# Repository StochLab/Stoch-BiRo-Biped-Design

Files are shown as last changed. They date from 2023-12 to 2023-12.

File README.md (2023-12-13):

# Design of Stoch BiRo (Bipedal Robot)

This repository provides the design files for [Stoch-BiRo](https://tayalmanan28.github.io/Stoch-BiRo/) [(Paper)](https://arxiv.org/pdf/2312.06512.pdf)

<div align="center">
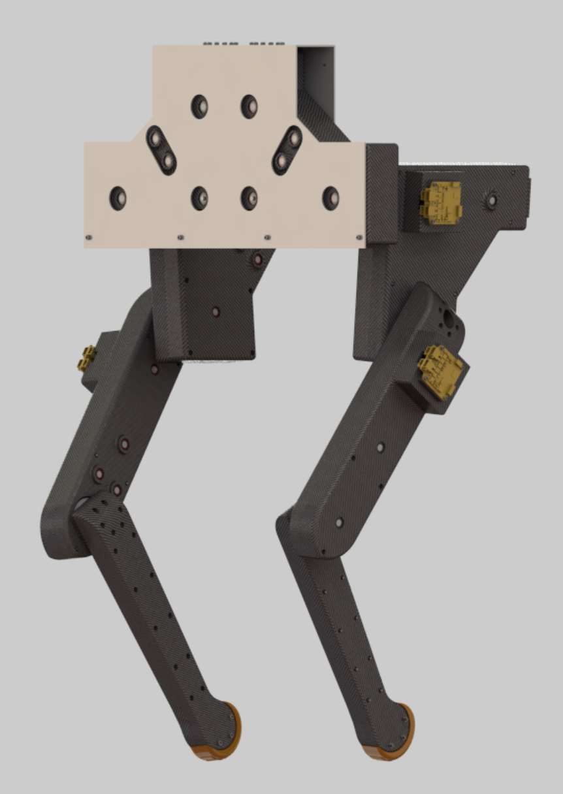
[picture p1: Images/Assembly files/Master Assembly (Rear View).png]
  <br>
<!--   <strong>Stoch BiRo</strong> -->
</div>

The Biped consists of a Torso and two 3-DOF Legs as described below:

<div align="center">
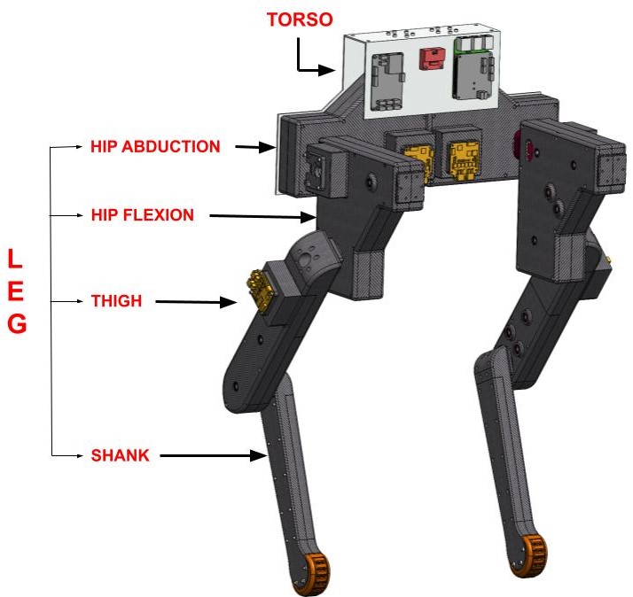
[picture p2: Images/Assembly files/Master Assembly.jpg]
  
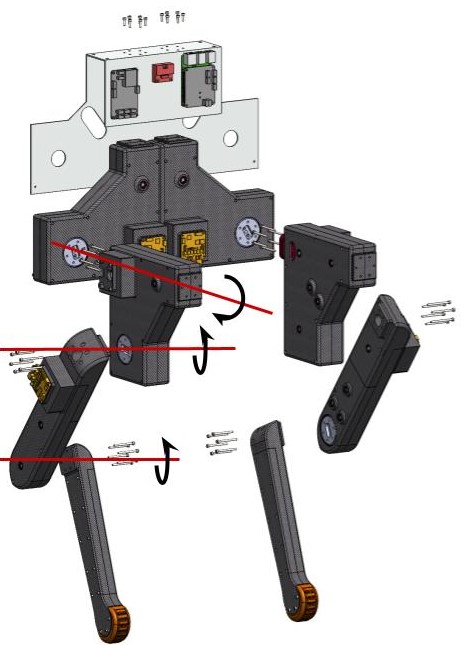
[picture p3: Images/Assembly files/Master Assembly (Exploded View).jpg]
    
</div>

## Torso

The torso consists of two L-shaped aluminum plates bolted together. The torso contains the Power Distribution Board, Raspberry Pi + Pi3Hat for on board compute, and sensors like Xsens MTi-610 IMU. 

## 3 DOF Leg

The hip actuator modules for both legs are mirrored versions of each other. 

**NOTE:** *The components in the actuation modules are denoted in the images below as follows:*

<div class="tg-wrap" align="center"><table align="center" style="margin: 0px auto;"><tbody><tr align="center"><td><strong>A.</strong></td><td><strong>B.</strong></td><td><strong>C.</strong></td><td><strong>D.</strong></td><td><strong>E.</strong></td><td><strong>F.</strong></td></tr><tr align = "center"><td>T-Motor Antigravity MN5006 BLDC Motor</td><td>Motor coupling</td><td>Stage-I HTD Pulley (13 Teeth)</td><td>MJBOTS Moteus r4.11 driver</td><td>HTD Timing Belts</td><td>Stage-II HTD Pulley (13 Teeth)</td></tr><tr align="center"><td><strong>G.</strong></td><td><strong>H.</strong></td><td><strong>I.</strong></td><td><strong>J.</strong></td><td><strong>K.</strong></td></tr><tr align = "center"><td>Stage-I HTD Pulley (39 Teeth)</td><td>Roller Tensioners</td><td>Stage-II HTD Pulley (39 Teeth)</td><td>Joint coupling</td><td> Hip-to-hip attachment</td></tr></tbody></table></div>

### Abduction Module

The abduction module is the topmost module of a leg in the biped. It is responsible for the abduction and adduction movement of the robot's hip, similar to that of humans. The module is attached to the torso plate and the motor drives the belts and pulleys with the output pulley attached to the abduction-flexion coupling. This coupling is a part of the abduction joint, which connects the abduction and the flexion modules. Tensioners are provided to prevent any slack in the timing belts while running.

<div align="center">
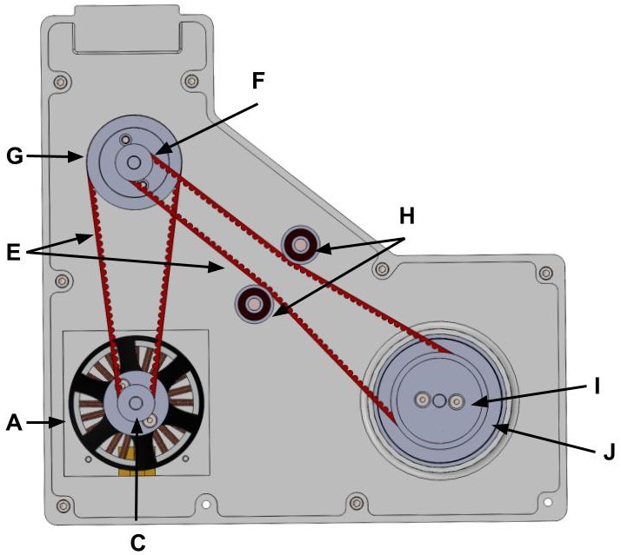
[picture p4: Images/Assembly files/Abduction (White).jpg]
  <br>
  <strong>Abduction Module</strong>
</div>

### Hip Flexion Module

The hip flexion module is placed between the hip abduction and thigh modules. This module is similar to that of the abduction module with few changes. It performs the flexion-extension motion. The motion of this module is controlled by the abduction motor and the motor in the flexion module controls the flexion joint, which connects the flexion and thigh modules. This module consists of a hip-to-hip attachment and the abduction-flexion coupling in the abduction module is fastened to it during assembly for transmitting the motion. The output pulley is connected to a flexion-thigh coupling. This coupling forms the flexion joint, which connects the flexion and thigh modules.

<div align="center">
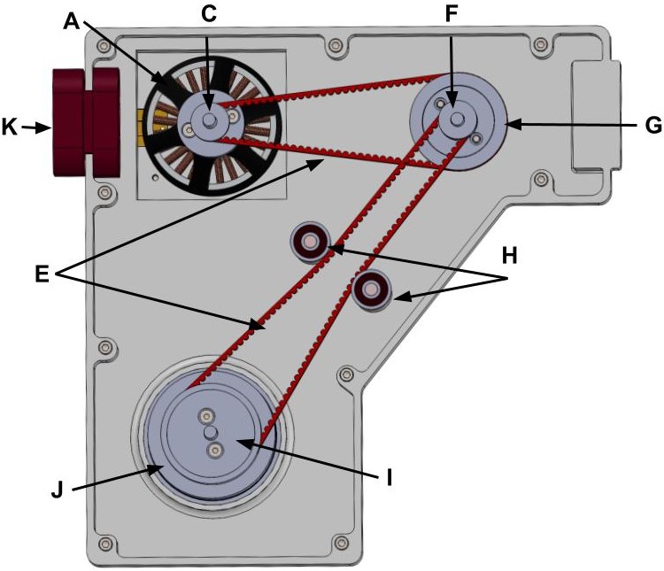
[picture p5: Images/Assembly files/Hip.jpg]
  <br>
  <strong>Hip Flexion Module</strong>
</div>

### Thigh Module

The thigh module is responsible for the knee motion of the biped, similar to the primary movement of human knees. The flexion joint controls the movement of this module. The motor of the thigh module, together with the dual-stage reduction using belts and pulleys, controls the knee joint. The thigh joint comprises a thigh-shank coupling, which is the same as that of the flexion-thigh coupling. The output pulley is attached to this coupling and the motion is transmitted to the shank module. Unlike the previous two modules which had a triangular configuration, the belts of this module are arranged linearly.

<div align="center">
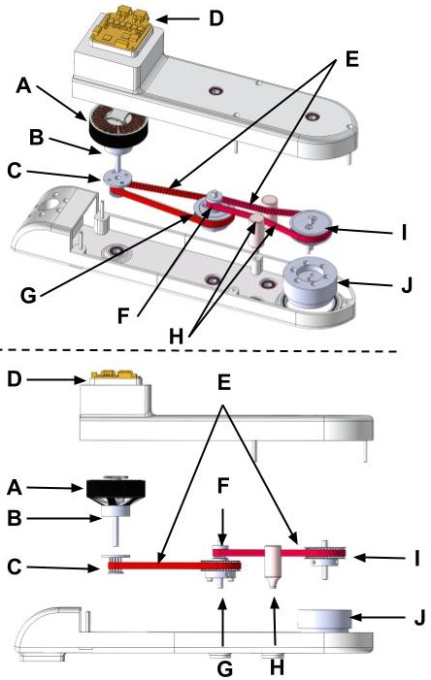
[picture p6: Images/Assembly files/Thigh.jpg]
  <br>
  <strong>Thigh Module</strong>
</div>

Internal components of the actuator modules are described here: 

- [Mechanical Components](https://github.com/StochLab/Stoch-BiRo-Biped-Design/blob/main/Mechanical%20components.md)
- [Electrical Components and Sensor Details](https://github.com/StochLab/Stoch-BiRo-Biped-Design/blob/main/Electrical%20Components.md)

### Shank

As the name suggests, the shank is the lowest part of the biped leg, which runs from the knee to the foot. The motor of the thigh controls its movement at the knee joint. A single-point contact foot made of polyurethane (PU) is attached to the end of the shank for better grip of the biped when in contact with a surface. This module is similar to the structure of the thigh but without any of the actuating components (motors, belts, pulleys, etc.) and with a provision for foot attachment at its bottom end.

<div align="center">
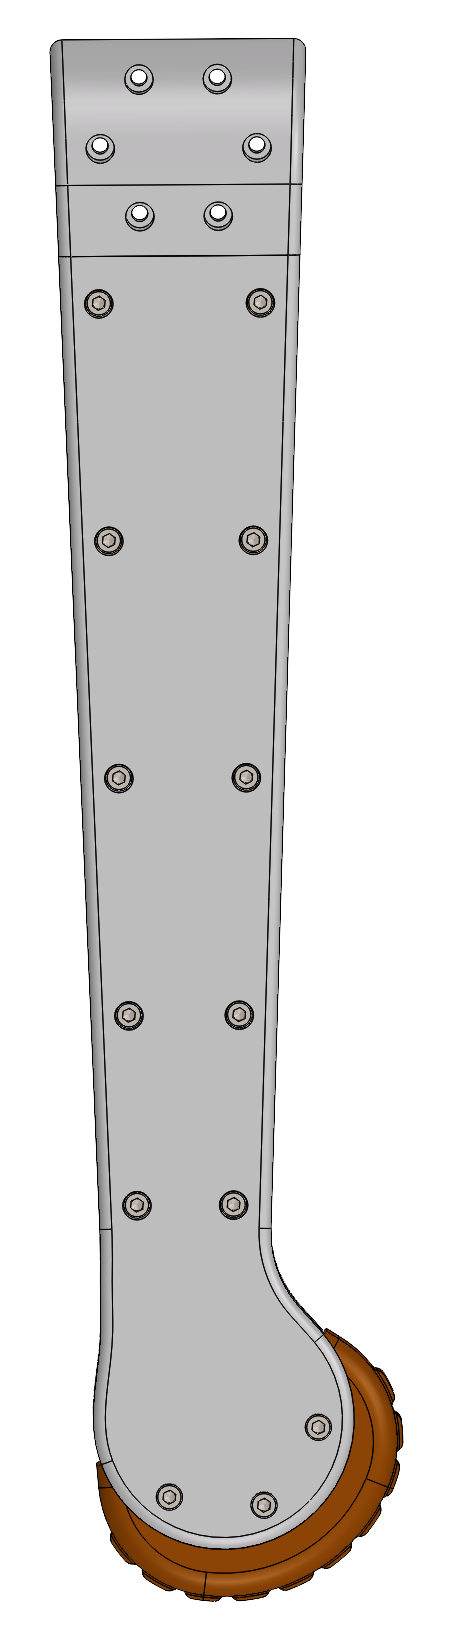
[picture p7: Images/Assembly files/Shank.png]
  <br>
  <strong>Shank</strong>
</div>

# Citation

If you use these designs and/or Stoch BiRo in your work please cite this paper with:

```
@misc{mothish2023stoch,
      title={Stoch BiRo: Design and Control of a low cost bipedal robot}, 
      author={GVS Mothish and Karthik Rajgopal and Ravi Kola and Manan Tayal and Shishir Kolathaya},
      year={2023},
      eprint={2312.06512},
      archivePrefix={arXiv},
      primaryClass={cs.RO}
}
```

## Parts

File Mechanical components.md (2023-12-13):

## Timing Belts and Pulleys:

HTD Timing belts made of Neoprene Rubber With Fiberglass Core, along with timing pulleys made of Aluminium, are responsible for increasing the torque by nine times. As the pulleys have 20 teeth and 60 teeth, two pairs of pulleys are used consecutively for an overall gear reduction of 9:1 with a 3:1 reduction at each stage. The HTD pulleys were 3D printed with an extra fine layer height of 0.1mm and 90\% infill density with PLA material and PVA (Polyvinyl acetate) supports as it is water soluble which facilitates support removal without any effect on the quality of tooth profile.

<div class="tg-wrap" align="center"><table align="center" style="margin: 0px auto;"><thead><tr><th colspan="6">HTD Timing Belts</th></tr></thead><tbody><tr align = "center"><td>Sl. No. </td><td>Pitch</td><td>Width</td><td>Total Length</td><td>Belt Height</td><td>Tooth Height</td></tr><tr align = "center"><td>1.</td><td>3mm</td><td>6mm</td><td>279mm</td><td>2.4mm</td><td>1.17mm</td></tr><tr align = "center"><td>2.</td><td>3mm</td><td>6mm</td><td>399mm</td><td>2.4mm</td><td>1.17mm</td></tr></tbody></table></div>

<div class="tg-wrap" align="center"><table style="margin-left: auto; margin-right: auto;"><thead><tr><th colspan="4">HTD Pulleys</th></tr></thead><tbody><tr align = "center"><td>Sl. No. </td><td>Bore Diameter</td><td>Outer Diameter</td><td>No. of Teeth</td></tr><tr align = "center"><td>1.</td><td rowspan="4">5mm</td><td rowspan="2">16mm</td><td>13</td></tr><tr align = "center"><td>2.</td><td>14</td></tr><tr align = "center"><td>3.</td><td rowspan="2">44mm</td><td>39</td></tr><tr align = "center"><td>4.</td><td>42</td></tr></tbody></table></div>

## Bearings:

Deep groove ball bearings are used as they are easy to mount and can accommodate both axial and radial loads. They have low friction and are optimized for low noise and low vibration which enables high rotational speeds. These bearings have minimal service or maintenance. The deep grooves in the bearings enable axial loads to be carried in either direction.

<div class="tg-wrap" align="center"><table><thead><tr><th colspan="4">Bearings</th></tr></thead><tbody><tr align = "center"><td>Sl. No. </td><td>Inner Diameter</td><td>Outer Diameter</td><td>Width</td></tr><tr align = "center"><td>1.</td><td>5mm</td><td>16mm</td><td>5mm</td></tr><tr align = "center"><td>2.</td><td>45mm</td><td>55mm</td><td>5mm</td></tr></tbody></table></div>

## Roller Tensioners:

Two tensioners are provided in each module to avoid any slack in the timing belts during its motion. As the motors are engaged, slippage between the pulley teeth and the belt teeth is possible. Tensioners act as rollers and provide tension to the belts resulting in proper teeth engagement between the belts and the pulleys. The tensioners used for the biped are long cylindrical structures attached to the bearings in the cover parts of the modules, which have moving components. They are placed so that it doesn't interfere with the working of an actuating system. The narrower cylindrical section of the tensioner is attached to the ball bearing.

## Motor Couplings:

The custom-made motor coupling connects the motor to the pulleys. 4 countersunk screws of M3 size are used to tighten the motor coupling to the motor's rotor. The shaft is attached to the motor coupling and the pulley of 20 teeth is locked to the shaft. The threaded holes are 18mm apart diagonally and the shaft is 5mm in diameter. The material used is stainless steel, as aluminum parts tend to bend, and steel is three times stronger than aluminum. Since the motor coupling is responsible for transmitting power from the motor to the rest of the actuation module, it is necessary to have a stronger material for the motor coupling.

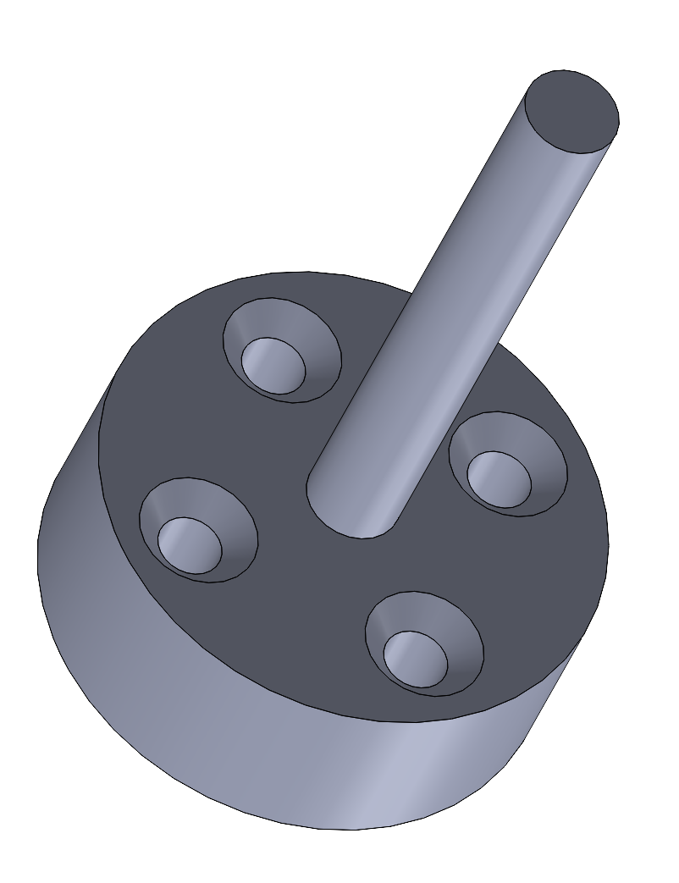
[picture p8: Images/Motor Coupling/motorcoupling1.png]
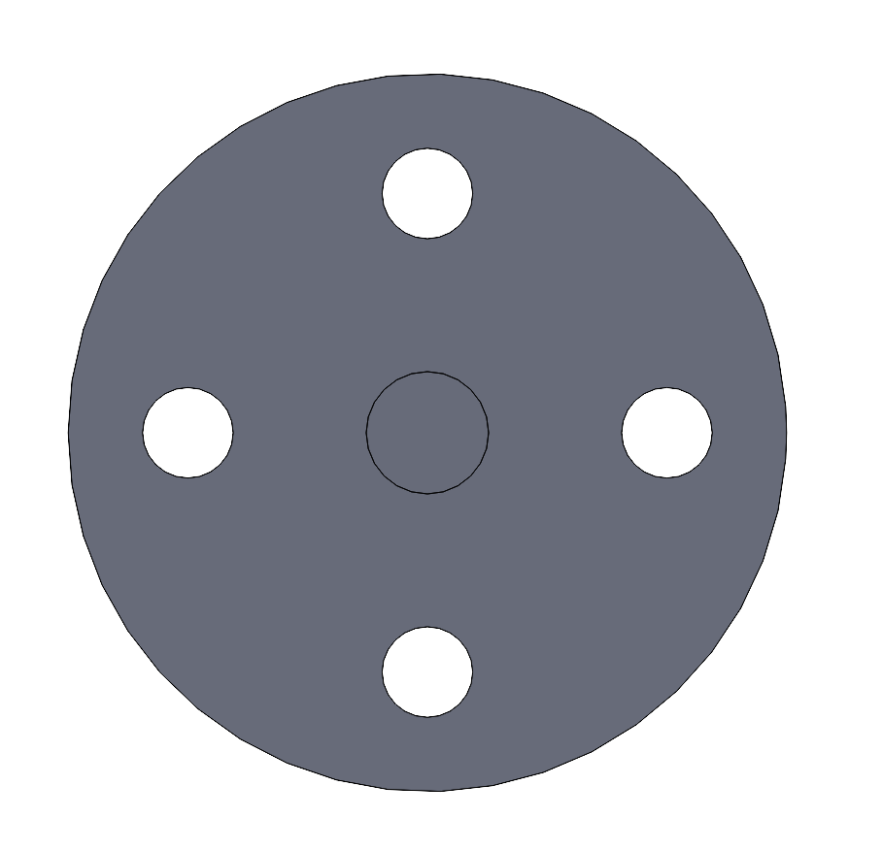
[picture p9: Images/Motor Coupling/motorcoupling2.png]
| |    |
|:---:|:---:|
|CAD Model|Rear View|

## Hip-to-hip attachment:

The hip-to-hip attachment, along with abduction-flexion coupling, connects the abduction module to the flexion module. Both modules are bolted to each other from the side of the abduction module. During the assembly of the modules, the hip-to-hip attachment is on the side of the flexion module and the abduction-flexion coupling is in the abduction module. Six M3 screws are bolted from the coupling's side to ensure proper rotation of the flexion module once the abduction motor is engaged. This part is put in a slit provided in the base part of the flexion module as a loose fit and once they are bolted, it will restrict any sort of relative motion with the flexion module resulting in a revolute joint between abduction and flexion modules.

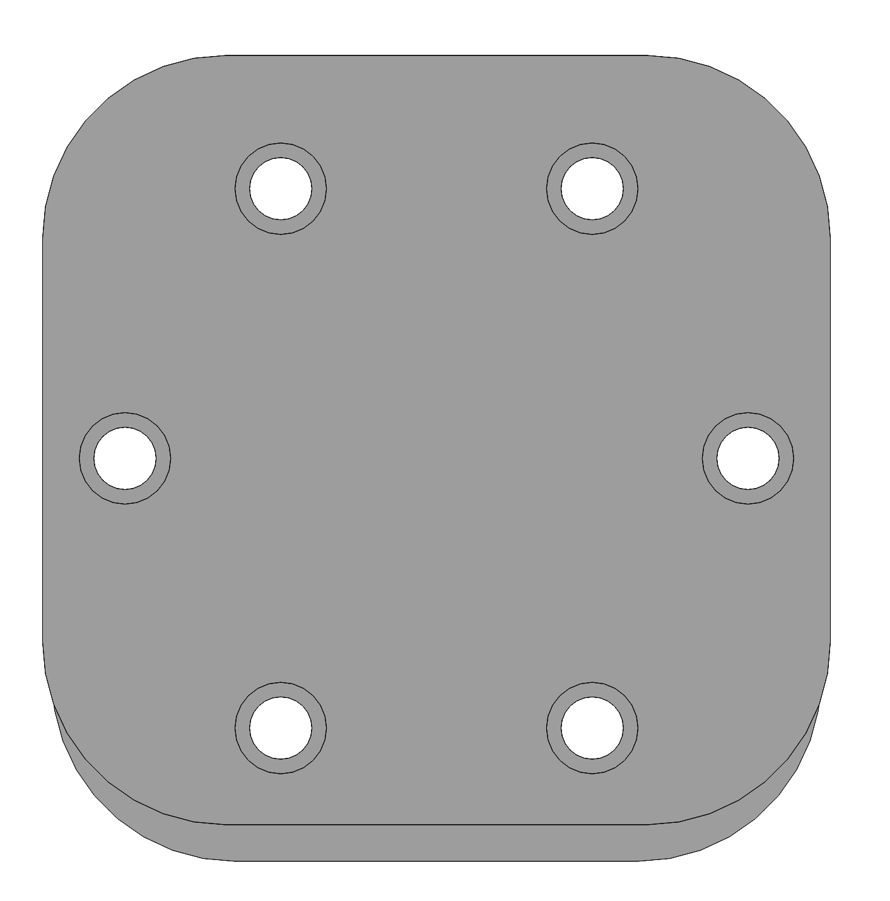
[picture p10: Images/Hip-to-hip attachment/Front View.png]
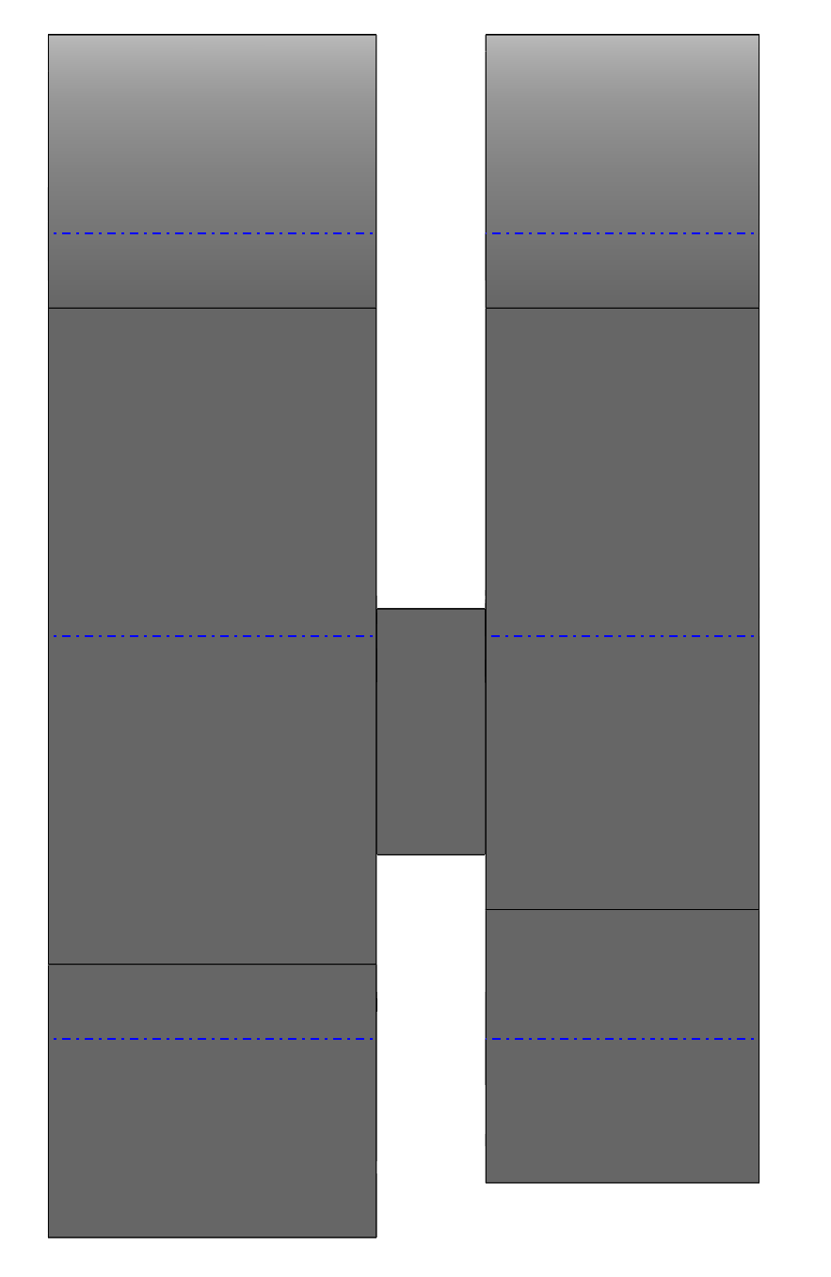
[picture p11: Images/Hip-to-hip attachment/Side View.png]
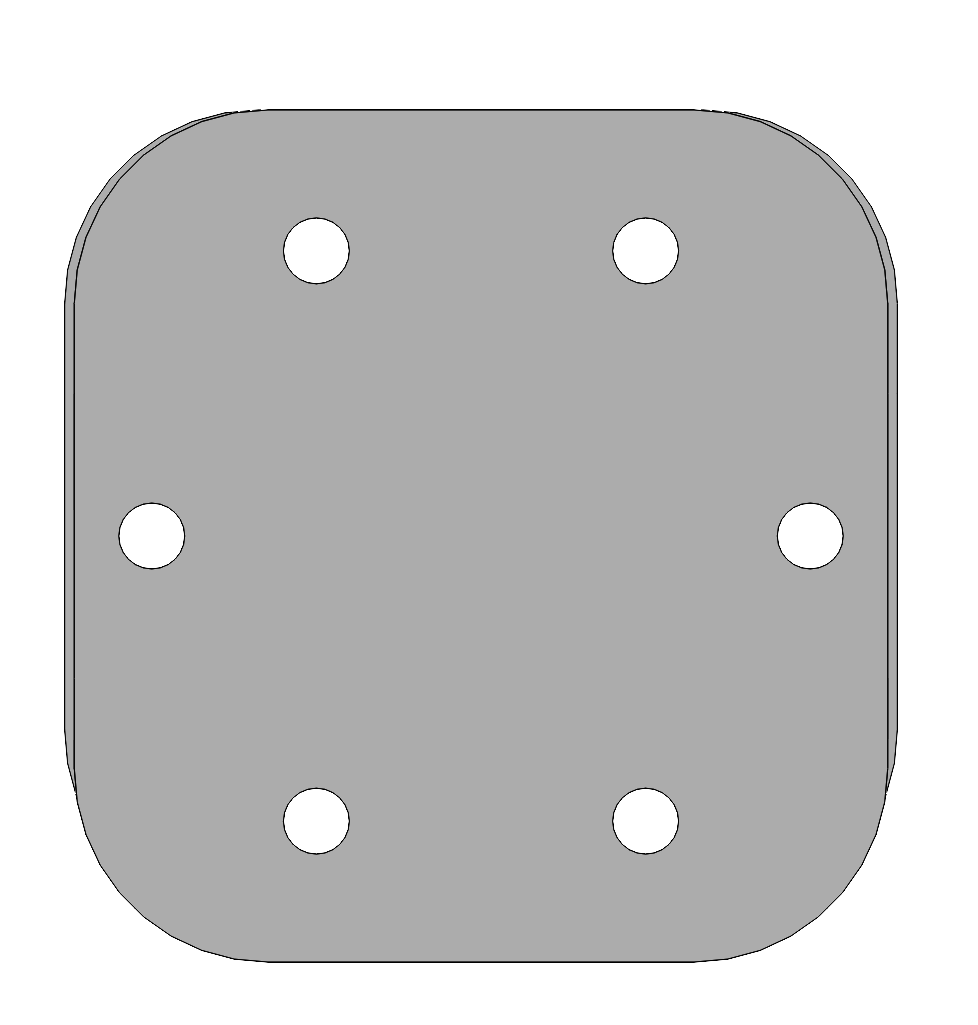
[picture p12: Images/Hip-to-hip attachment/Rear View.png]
| |    |  |
|:---:|:---:|:---:|
|Front View|Side View|Rear View|

## Joint Couplings:

The joint couplings are parts used to connect two actuator modules. Two such distinct couplings are used in the biped: abduction-flexion coupling and flexion-thigh coupling (thigh-shank coupling uses the same design). As the names suggest, abduction-flexion coupling acts as the joint between the hip abduction and flexion modules, flexion-thigh coupling as the joint between the hip flexion and thigh modules, and thigh-shank one as the joint between the thigh and shank modules. In all of them, the output pulley (the larger pulley of the second belt-pulley reduction stage) is bolted to the coupling using two M3 bolts (14mm apart diametrically). In the case of abduction-flexion coupling, the adjacent module, which is the flexion module, is bolted from the abduction module's side. Meanwhile, in the case of flexion-thigh and thigh-shank couplings, the adjacent modules (thigh and shank, respectively) are bolted from outside (i.e. side of the adjacent modules) using six M3 bolts.

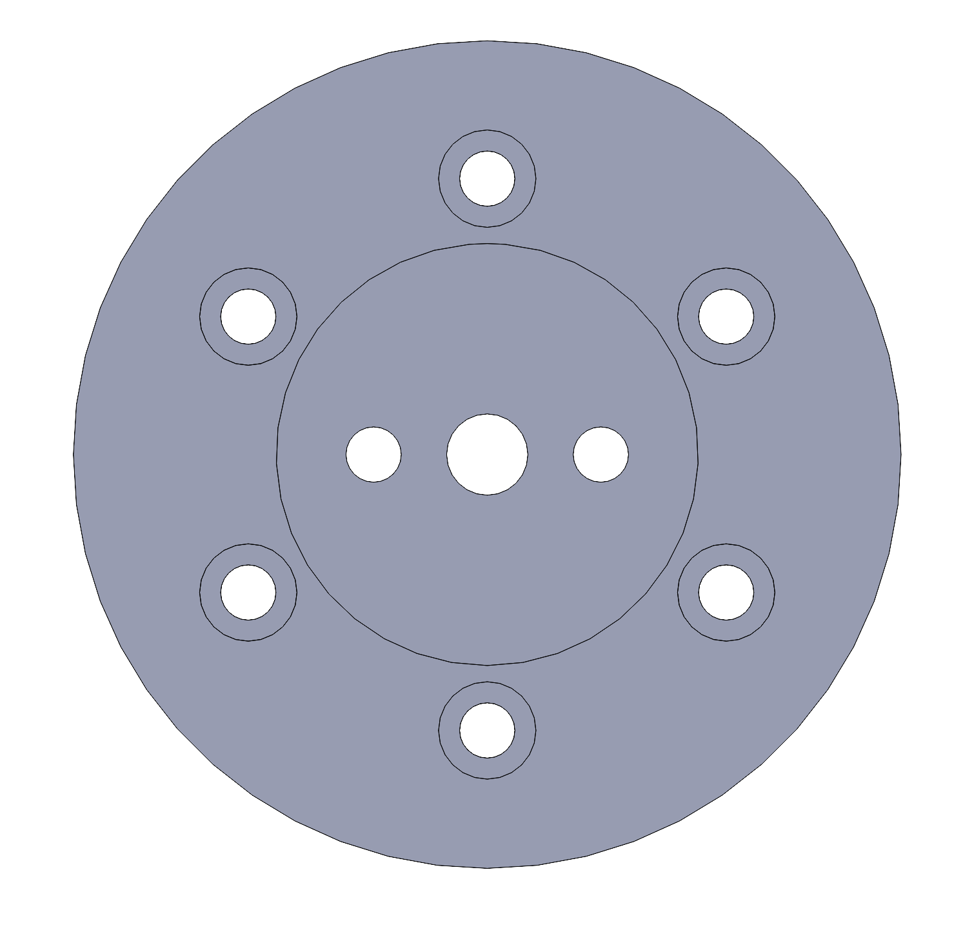
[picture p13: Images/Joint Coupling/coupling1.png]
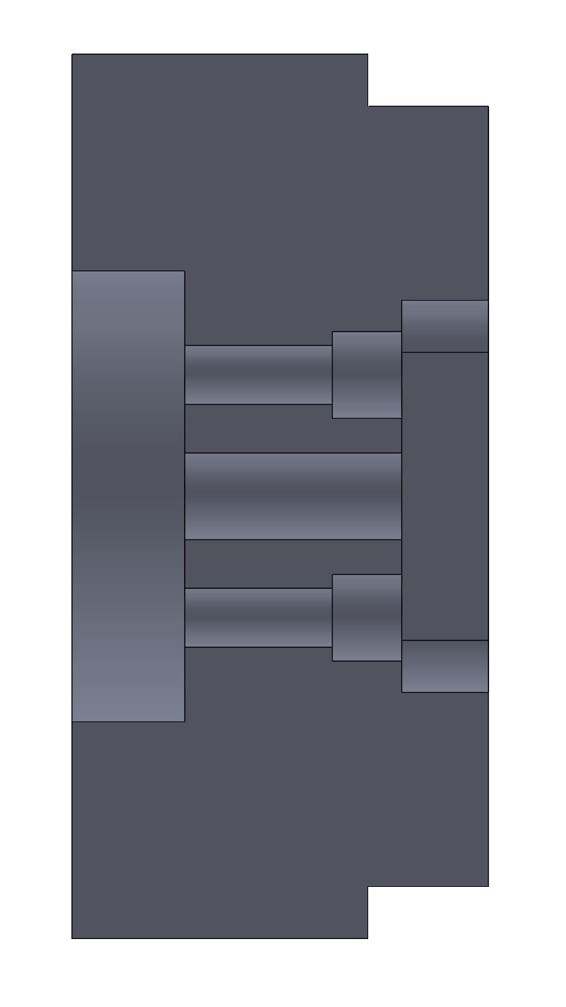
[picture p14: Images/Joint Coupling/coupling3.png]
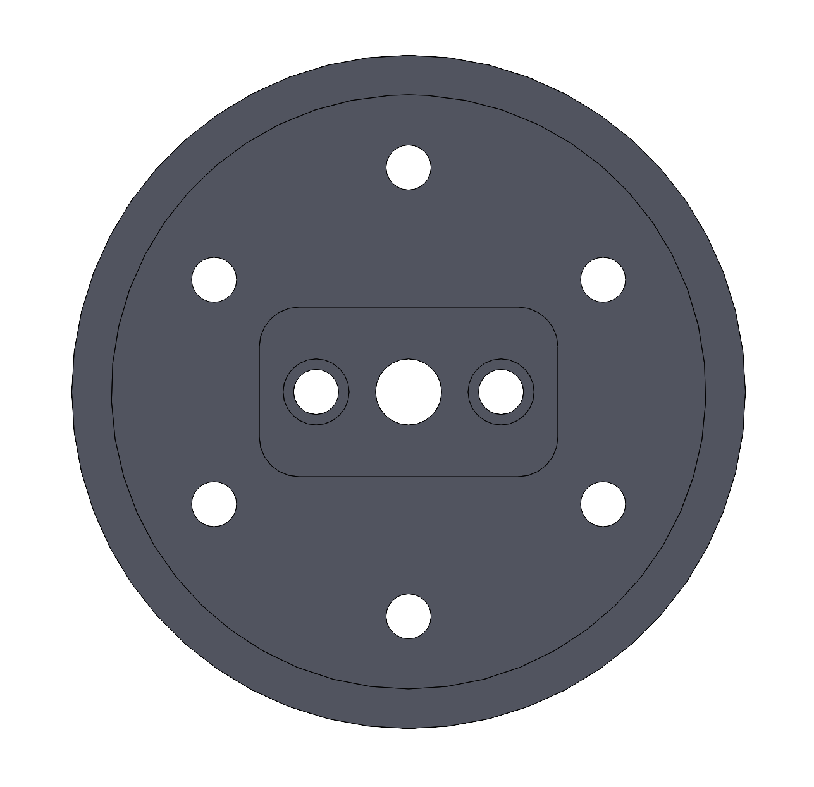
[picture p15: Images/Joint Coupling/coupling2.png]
| |    |  |
|:---:|:---:|:---:|
|Front View|Section View|Rear View|

## Foot:

The foot is made of PMC-780, a urethane rubber prepared by mixing Part A and Part B in a 2:1 ratio by weight or volume. Part A and Part B comprise resins and hardening agents, respectively. After mixing, they are poured into a mold with a constant flow rate to avoid bubble formation. The mixture is then undisturbed for 48 hours, after which it is removed from the mold. The mold is to be sprayed with a heavy-duty silicone spray before pouring the mixture for easier detachment from the mold surface after solidification.

| |    |
|:---:|:---:|
|CAD Model of the Foot|CAD Model of the Mould|

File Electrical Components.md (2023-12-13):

## Brushless DC Motor

T-Motor Antigravity MN5006 KV300 brushless DC motor is used for each actuation module; therefore in total six motors (3 for each leg). Brushless DC motors provide more torque
per watt of power drawn than brushed motors, thus making them more efficient. Controlling such motors are more efficient as they have better speed vs. torque characteristics and faster
dynamic response. KV300 here indicates the motor performs 300 revolutions per minute (RPM) per Volt that is given as input. 

<div class="tg-wrap" align="center"><table><thead><tr><th colspan="2">Motor Specifications</th></tr></thead><tbody><tr align = "center"><td>Motor Size</td><td>55.6mm * 30mm (OD * Width)</td></tr><tr align = "center"><td>Shaft Diameter</td><td>6mm</td></tr><tr align = "center"><td>KV</td><td>300</td></tr><tr align = "center"><td>Motor Weight</td><td>108g</td></tr><tr align = "center"><td>Peak Current (180s)</td><td>20A</td></tr><tr align = "center"><td>Maximum Power (180s)</td><td>500W</td></tr><tr align = "center"><td>Maximum Torque</td><td>0.5 N-m</td></tr></tbody></table></div>

| |    | 
|:---:|:---:|
|Front View|Rear View|

## Motor Driver

Mjbots' Moteus r4.11 driver controls the motor inputs. The Moteus controller is intended to drive 3-phase brushless motors using field-oriented control (FOC). It contains
three half-H bridges to switch power to each of the three phases, a built-in magnetic encoder to measure the rotor position, and current sensing capabilities on each of the three phases.
A magnet is attached to the shaft, part of the motor coupling. As the magnet rotates, the absolute magnetic encoder in the moteus driver records rotation by measuring the magnetic flux
density using the Hall Effect principle. The magnetic encoder provides essential feedback for maintaining precise control over the motor’s position, speed, and torque. By leveraging this
data, the Moteus driver ensures smooth and efficient operation of the brushless motor, enabling optimal performance in various applications. The magnetic encoder is seen as a black chip in
the center of the driver’s rearview. 

<div class="tg-wrap" align="center"><table><thead><tr><th colspan="2">Moteus r4.11 Driver Specifications</th></tr></thead><tbody><tr align="center"><td>Peak Phase Current</td><td>100A</td></tr><tr align="center"><td>Voltage Input</td><td>10-44V</td></tr><tr align="center"><td>KV</td><td>300</td></tr><tr align="center"><td>Temperature</td><td>-40 to 85 deg C</td></tr><tr align="center"><td>Peak Electrical Power</td><td>500W</td></tr><tr align="center"><td>Control Rate</td><td>15 - 30 kHz</td></tr></tbody></table></div>

| |    | 
|:---:|:---:|
|Front View|Rear View|

## Inertial Measurement Unit (IMU)

An inertial measurement unit (IMU) collects and outputs accelerometer, gyroscope, and magnetometer data, fully synchronized and calibrated. The IMU used in the biped is Xsens MTi-610 IMU. It is mounted on the torso plate to estimate the robot's position and orientation, or in other words, motion tracking. To facilitate seamless communication between the IMU and the robot's control systems, a Raspberry Pi serves as the intermediary, connecting the IMU via the Controller Area Network (CAN) protocol. This protocol ensures reliable and efficient data transmission, enabling real-time updates and integration of the IMU data into the robot's overall control framework.

| |    | 
|:---:|:---:|
|Xsens MTi-610 IMU|PDB|

## Power Distribution Board (PDB)

A power distribution board (PDB) is an important part of an electricity supply system. Its job is to split an incoming electrical power feed into multiple secondary or subsidiary circuits. When the motors start running, it draws a large amount of current from the battery, resulting in a large voltage drop across the connecting wires (wires are low ohmage resistors). This will cause the other electronics to face a large current drop. Here is where the power distribution board plays its role. 

The biped uses the MJBOTS r4.3b version of PDB. It incorporates pre-charging capabilities, energy monitoring functionality, and over-current protection mechanisms. These features contribute to a smoother power transition and prevent excessive current from negatively affecting other electronics. Furthermore, the PDB is equipped with a soft power switch, enabling convenient control over the power supply to the biped. It also facilitates power connector fanout, allowing for efficient power distribution to various subsystems and components. To enhance monitoring and control capabilities, the PDB integrates a CAN-FD port. This enables the host software to continuously monitor the state of the switch, input voltage, power, and energy levels. Additionally, it allows the software to request a "soft power down" to initiate a delayed shutdown, ensuring a controlled and orderly power-off process. Overall, the MJBOTS r4.3b PDB offers comprehensive functionality and protection measures, ensuring reliable power distribution and efficient management of the biped's electrical system.

## RPi \+ Pi3Hat

### Raspberry Pi

Raspberry Pi microcontroller is a type of single-board computer (SBC), meaning that its entire hardware set is placed on a single electronics board. It is unable to replace or add components because there are no CPU sockets, memory slots, or expansion buses like PCIe. A Raspberry Pi's board includes a CPU, RAM, LAN, USB, and micro HDMI connectors, as well as a micro SD card slot. Raspberry Pi is used to receive the data from the IMU in the biped and accordingly provide the motor inputs to the motor drivers.  

By acting as an interface between the IMU and the motor drivers, the Raspberry Pi enables the biped to effectively process the IMU data and translate it into appropriate motor commands. This facilitates precise control over the robot's movements and helps maintain stability and balance during operation. The compact size, versatile connectivity options, and ability to run various software platforms make the Raspberry Pi an ideal choice for integrating into the biped robot system. Its capability to handle data from the IMU and drive the motor drivers plays a crucial role in ensuring the biped's motion control and overall functionality.

### Pi3Hat

MJBOTS Pi3hat is a daughterboard for a Raspberry Pi, which provides a power input ranging from 8-44V, 5V for Raspberry Pi, and independent 5Mbps CAN-FD buses. Attaching the Pi3hat to the Raspberry Pi GPIO header will provide power input capabilities and facilitate communication interfaces (CAN-FD protocol is used for the biped) to make the robot control easier. It attaches to the Raspberry Pi's GPIO header and presents as a registered hat.

One of the notable features of the Pi3hat is its inclusion of independent 5Mbps CAN-FD buses. These CAN-FD buses serve as communication channels, utilizing the CAN-FD protocol, specifically employed for the biped application. This allows for seamless data exchange and control between the Raspberry Pi and other components or modules within the robot system. By connecting the Pi3hat to the Raspberry Pi, the Pi3hat effectively becomes a registered hat, tightly integrated with the Raspberry Pi's hardware and software ecosystem. This integration streamlines the overall robot control process, enabling efficient communication and power management, and simplifying the overall system architecture.

| |    |  |
|:---:|:---:|:---:|
|Raspberry Pi (RPi)|Pi3Hat|RPi + Pi3Hat|

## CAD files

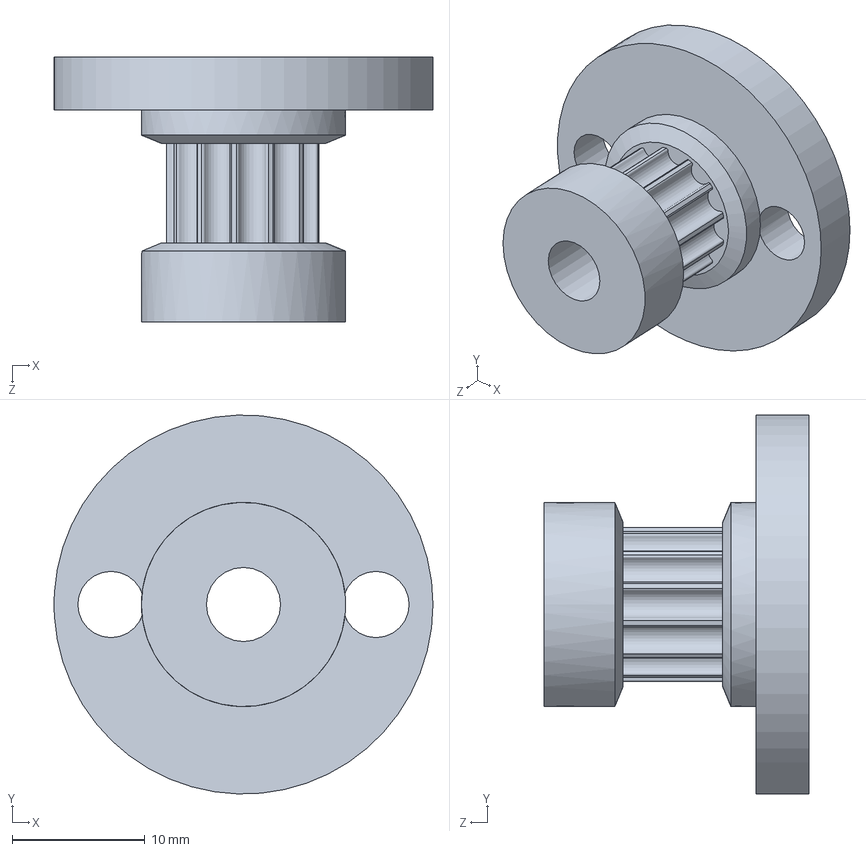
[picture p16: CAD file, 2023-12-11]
Design Files/SLDPRT & SLDASM/HTD (13 Teeth) - Middle.SLDPRT
28.6 x 28.6 x 20.0 mm

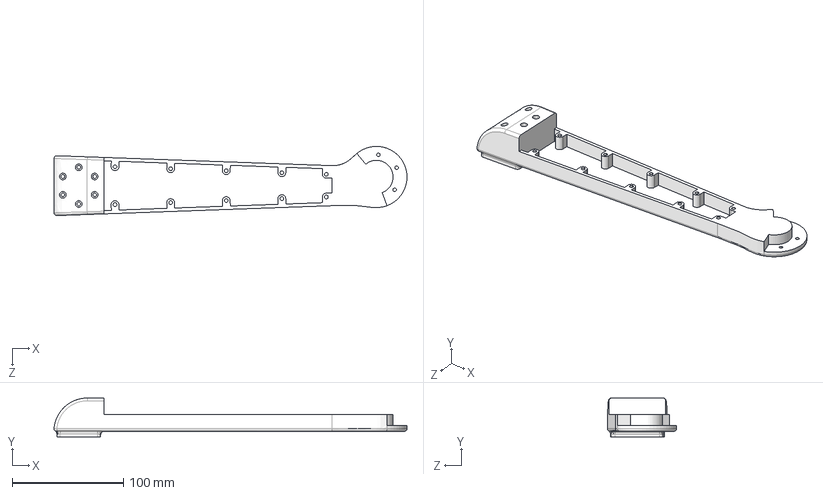
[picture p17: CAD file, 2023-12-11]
Design Files/STEP/Shank_Base.STEP
317.4 x 35.0 x 62.2 mm

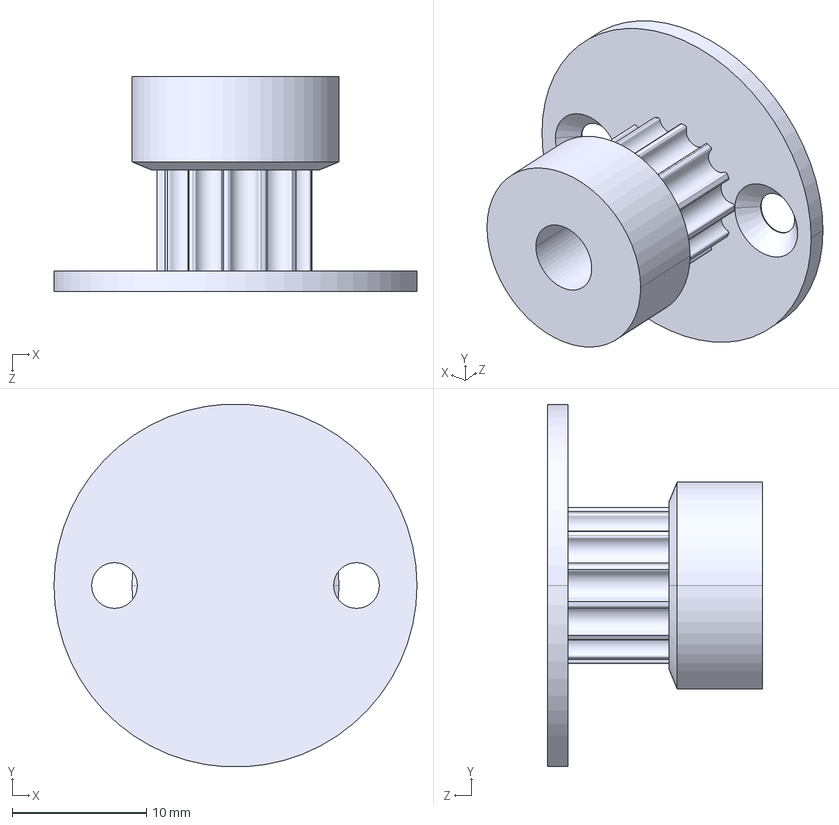
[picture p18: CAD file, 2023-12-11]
Design Files/STEP/MirrorHTD (13 Teeth)_GearTrax.STEP
27.0 x 27.0 x 16.0 mm

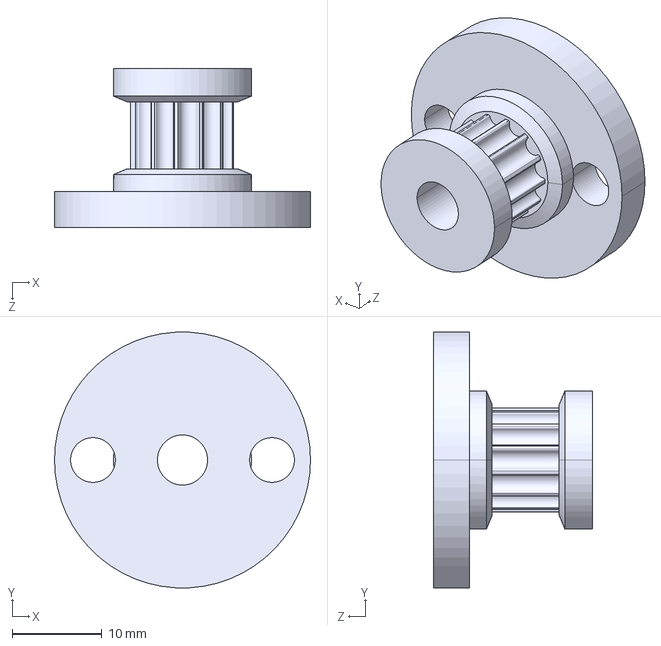
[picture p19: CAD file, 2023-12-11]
Design Files/STEP/MirrorHTD (13 Teeth) - Middle [Thigh]_GearTrax.STEP
28.6 x 28.6 x 17.7 mm

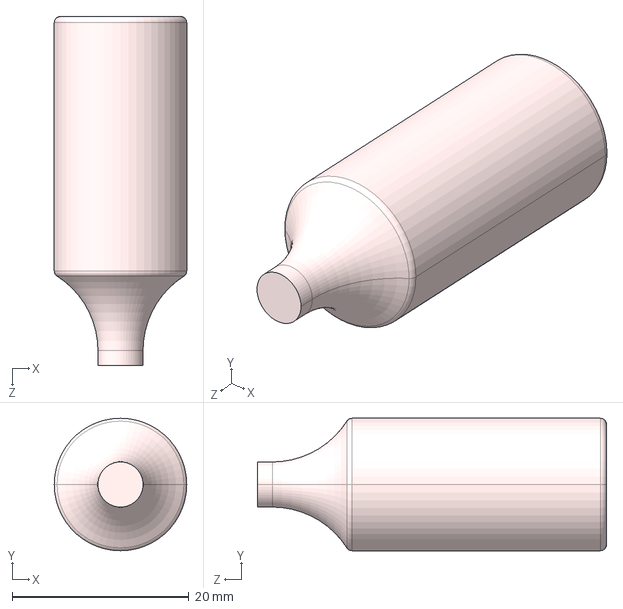
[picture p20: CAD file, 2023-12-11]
Design Files/STEP/Mirrorbelt tensioner.STEP
15.0 x 15.0 x 39.5 mm

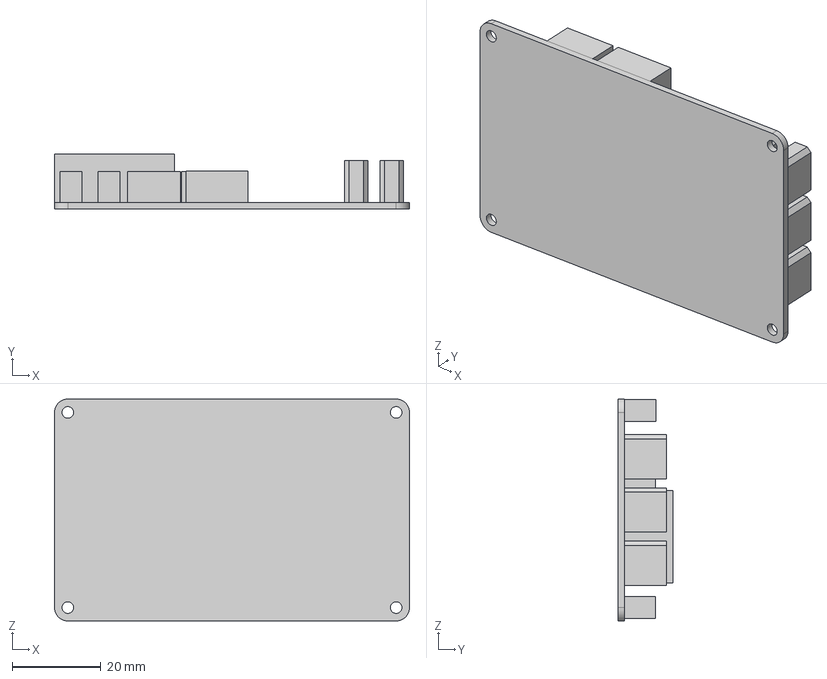
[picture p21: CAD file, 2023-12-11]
Design Files/SLDPRT & SLDASM/PDB.step
80.0 x 12.5 x 50.0 mm

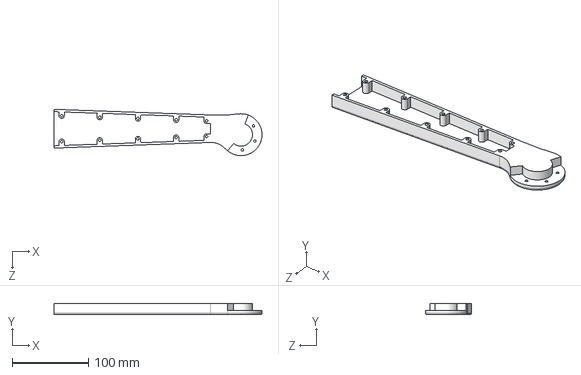
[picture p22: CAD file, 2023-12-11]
Design Files/STEP/Shank_Cover.STEP
272.5 x 15.0 x 60.7 mm

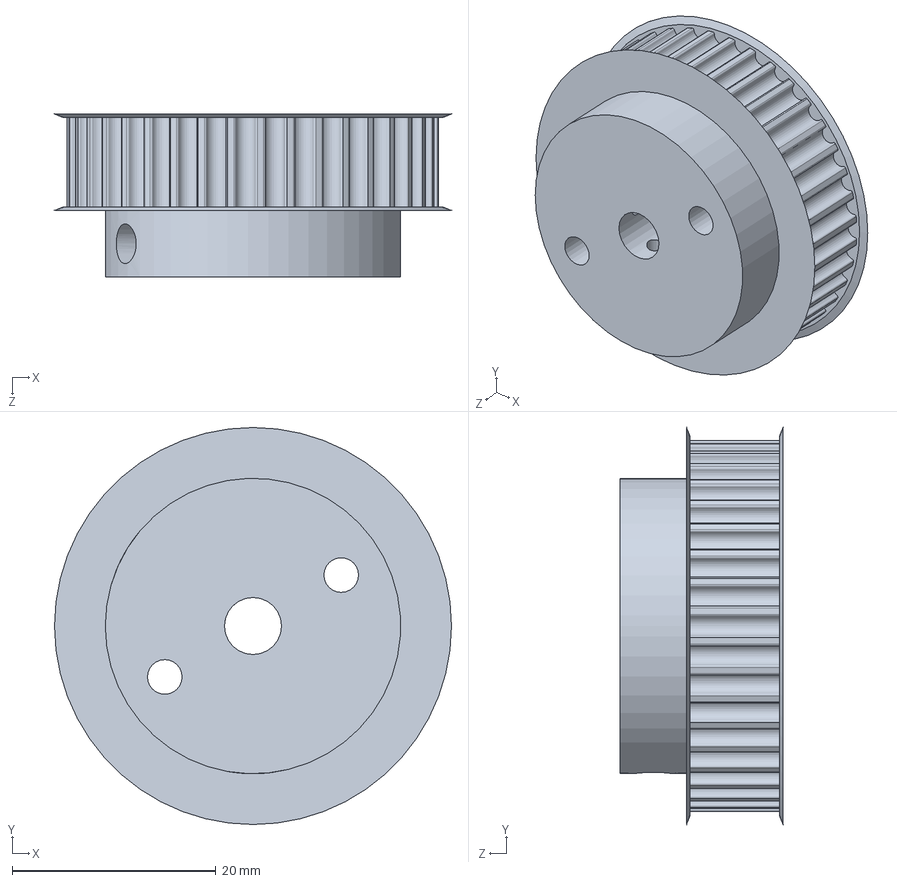
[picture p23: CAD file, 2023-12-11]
Design Files/SLDPRT & SLDASM/HTD (39 Teeth) - Middle.SLDPRT
39.0 x 39.0 x 16.0 mm

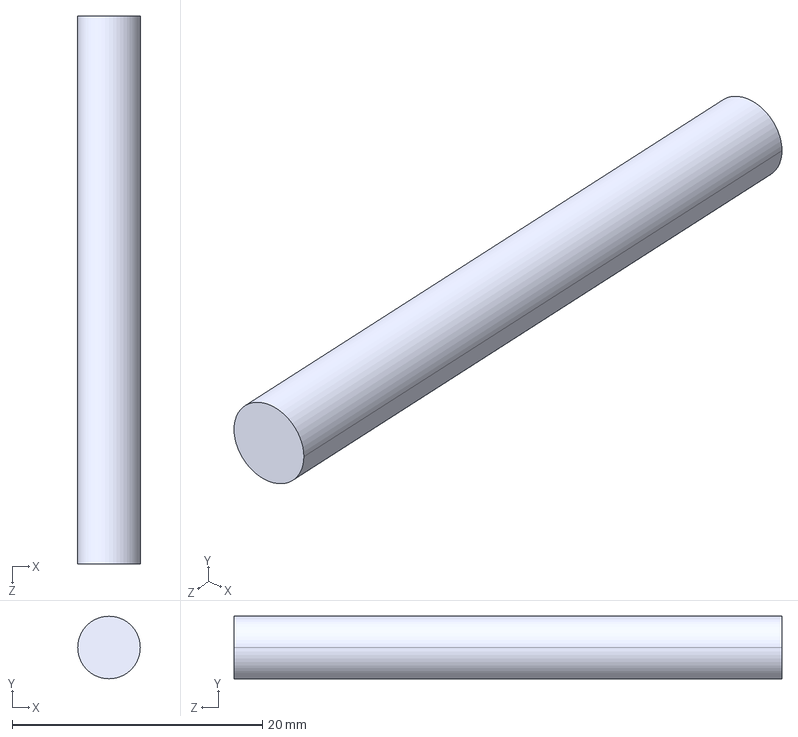
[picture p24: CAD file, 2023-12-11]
Design Files/STEP/5mm Shaft (Abd and Hip) - Driven.STEP
5.00 x 5.00 x 43.8 mm

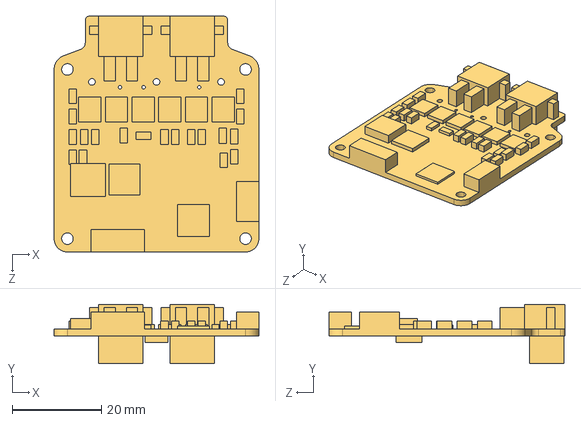
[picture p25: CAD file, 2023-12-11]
Design Files/STEP/MirrorMoteus_r4.11.STEP
46.0 x 13.4 x 53.0 mm

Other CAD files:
Design Files/STEP/Master Assembly.STEP
Design Files/SLDPRT & SLDASM/MirrorHTD (39 Teeth).SLDPRT
Design Files/SLDPRT & SLDASM/MirrorHTD (13 Teeth) - Thigh.SLDPRT
Design Files/SLDPRT & SLDASM/MirrorHTD (39 Teeth)1.SLDPRT
Design Files/SLDPRT & SLDASM/HTD (13 Teeth) - Middle [Thigh].SLDPRT
Design Files/SLDPRT & SLDASM/MirrorHTD (13 Teeth) - Middle1.SLDPRT
Design Files/STEP/Shank_Left.STEP
Design Files/SLDPRT & SLDASM/MirrorHTD (39 Teeth) - Middle1.SLDPRT
Design Files/SLDPRT & SLDASM/3D printed part (hip2hip).SLDPRT
Design Files/SLDPRT & SLDASM/3D printed part .SLDPRT
Design Files/SLDPRT & SLDASM/5mm Shaft (Abd and Hip) - Driven.SLDPRT
Design Files/SLDPRT & SLDASM/5mm Shaft (Abd and Hip).SLDPRT
Design Files/SLDPRT & SLDASM/5mm Shaft (Thigh) - Driven.SLDPRT
Design Files/SLDPRT & SLDASM/5mm Shaft (Thigh).SLDPRT
Design Files/SLDPRT & SLDASM/Bearing (45 X 55 X 6 mm).SLDPRT
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
